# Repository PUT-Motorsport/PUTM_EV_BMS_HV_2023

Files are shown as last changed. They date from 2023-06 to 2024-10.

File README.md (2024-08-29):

# PUTM_EV_BMS_HV_MASTER_2023
Accumulator Managment System (High Voltage Battery Managment System)

## Overview
The AMS system consists of two main parts, the master and multiple slaves.
<p align="center">
  
</p>
The apparatus is responsible for the managment of the battery as a whole, determining it's states like: state of charge or unsafe state plausibility. It also supervises the turning on and off of the hv bus.

## Master
The AMS Master is the center of the whole system it's responsible for most of the tasks: current measurement, high voltage relay control, slave control, high voltage measurement and communication with the car. 
<p align="center"> 
  
</p>

### Software
The AMS system havely relies on RTOS (Real Time Operating System) for seperating and managing different tasks. The system is divided mainly into three parts:
- main task - responsible for control over the whole system,
- subsidiary tasks - for off handling time consuming calculations or interfacing,
- communication tasks - for handling communication with external systems like CAN communication with the car or isoSPI for communication with the slaves.

### Hardware 
The AMS is powered by STM32G484xx, a powerful, new gen MCU capable of handling varius communication interfaces and tasks. On board there are also three 24bit ADC ICs responsible for taking precise measurments of flowing current and voltage present on HV bus. For interfacing with other components the AMS uses M80 and M300 series Harwin connectors which offer high reliability. The board also features other logic components all on a custom 4 layer board.

<p align="center"> 
  
</p>

### The research and development work was carried out was a part of the Student Scientific Clubs Create Innovations (SKNTI) program. [Ministry of Science and Higher Education](https://www.gov.pl/web/nauka)
baner-sknti

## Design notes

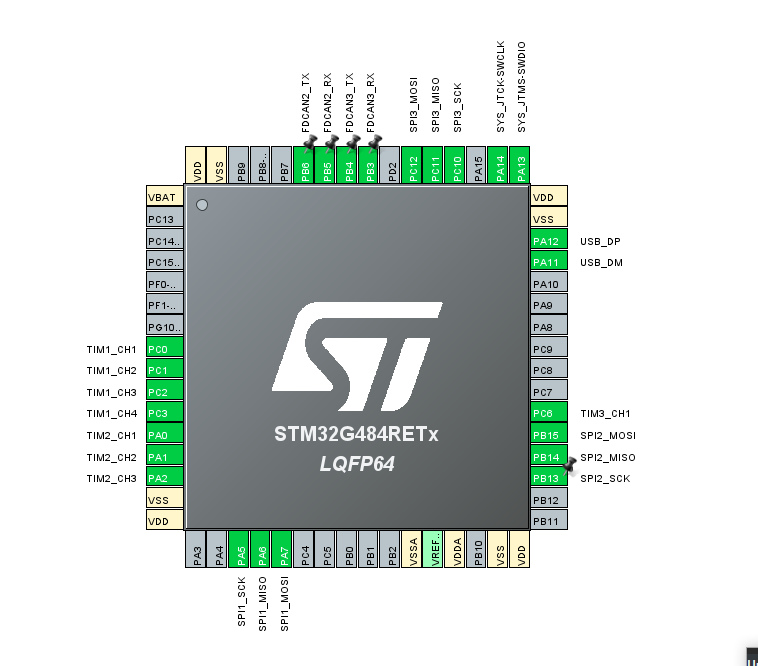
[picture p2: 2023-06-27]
hardware/images/Zrzut ekranu 2023-05-05 002628.png

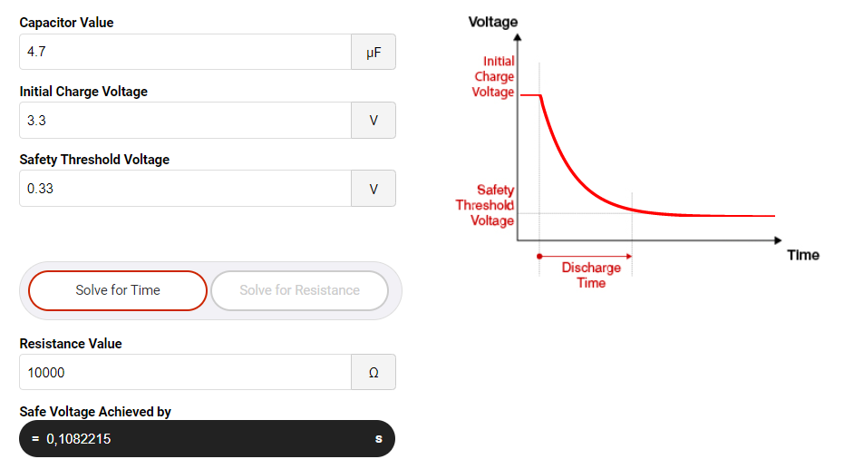
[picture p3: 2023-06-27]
hardware/images/peak_generator_graph.png

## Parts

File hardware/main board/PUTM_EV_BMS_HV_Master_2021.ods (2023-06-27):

Source: | C:\Users\Tomek\Desktop\PUTM\2021\BMS master\PUTM_EV_BMS_HV_Master_2021\PUTM_EV_BMS_HV_Master_2021.sch
Date: | 21.05.2021 00:54:58
Tool: | Eeschema (5.1.5)-3
Generator: | C:\Program Files\KiCad\bin\scripting\plugins/bom_csv_grouped_by_value.py
Component Count: | 206
Individual Components:
Item | Qty | Reference(s) | Value | LibPart | Footprint | Datasheet | MF | PARTREV | STANDART
 |  | BT1 | KEYSTONE 103 | Device:Battery_Cell | Battery:BatteryHolder_Keystone_103_1x20mm | ~
 |  | C1 | 100nF | Device:C | Capacitor_SMD:C_0603_1608Metric | ~
 |  | C2 | 680uF/35V | Device:CP_Small | Capacitor_SMD:CP_Elec_8x10 | ~
 |  | C3 | 4.7uF | Device:C_Small | Capacitor_SMD:C_0603_1608Metric | ~
 |  | C4 | 100nF | Device:C | Capacitor_SMD:C_0603_1608Metric | ~
 |  | C5 | 4.7uF | Device:C_Small | Capacitor_SMD:C_0603_1608Metric | ~
 |  | C6 | 1nF/1kV | Device:C | Capacitor_SMD:C_1206_3216Metric | ~
 |  | C7 | 1nF/1kV | Device:C | Capacitor_SMD:C_1206_3216Metric | ~
 |  | C8 | 220uF/35V | Device:CP_Small | Capacitor_SMD:CP_Elec_8x10 | ~
 |  | C9 | 10uF | Device:C_Small | Capacitor_SMD:C_0603_1608Metric | ~
 |  | C10 | 10uF | Device:C_Small | Capacitor_SMD:C_0603_1608Metric | ~
 |  | C11 | 100nF | Device:C | Capacitor_SMD:C_0603_1608Metric | ~
 |  | C12 | 100nF | Device:C | Capacitor_SMD:C_0603_1608Metric | ~
 |  | C13 | 1uF | Device:C_Small | Capacitor_SMD:C_0603_1608Metric | ~
 |  | C14 | 1uF | Device:C_Small | Capacitor_SMD:C_0603_1608Metric | ~
 |  | C15 | 100nF | Device:C_Small | Capacitor_SMD:C_0603_1608Metric | ~
 |  | C16 | 1uF | Device:C_Small | Capacitor_SMD:C_0603_1608Metric | ~
 |  | C17 | 1uF | Device:C_Small | Capacitor_SMD:C_0603_1608Metric | ~
 |  | C18 | 100nF | Device:C | Capacitor_SMD:C_0603_1608Metric | ~
 |  | C19 | 100nF | Device:C_Small | Capacitor_SMD:C_0603_1608Metric | ~
 |  | C20 | 100nF | Device:C_Small | Capacitor_SMD:C_0603_1608Metric | ~
 |  | C21 | 22pF | Device:C_Small | Capacitor_SMD:C_0805_2012Metric | ~
 |  | C22 | 22pF | Device:C_Small | Capacitor_SMD:C_0805_2012Metric | ~
 |  | C23 | 10uF | Device:C_Small | Capacitor_SMD:C_0603_1608Metric | ~
 |  | C24 | 4.7uF | Device:C_Small | Capacitor_SMD:C_0603_1608Metric | ~
 |  | C25 | 1uF | Device:C_Small | Capacitor_SMD:C_0603_1608Metric | ~
 |  | C26 | 100nF | Device:C_Small | Capacitor_SMD:C_0603_1608Metric | ~
 |  | C27 | 100nF | Device:C_Small | Capacitor_SMD:C_0603_1608Metric | ~
 |  | C28 | 100nF | Device:C_Small | Capacitor_SMD:C_0603_1608Metric | ~
 |  | C29 | 10uF | Device:C_Small | Capacitor_SMD:C_0603_1608Metric | ~
 |  | C30 | 10uF | Device:C_Small | Capacitor_SMD:C_0603_1608Metric | ~
 |  | C31 | 100nF | Device:C_Small | Capacitor_SMD:C_0603_1608Metric | ~
 |  | C32 | 10uF | Device:C_Small | Capacitor_SMD:C_0603_1608Metric | ~
 |  | C33 | 1uF | Device:C_Small | Capacitor_SMD:C_0603_1608Metric | ~
 |  | C34 | 4.7uF | Device:C_Small | Capacitor_SMD:C_0603_1608Metric | ~
 |  | C35 | 100nF | Device:C_Small | Capacitor_SMD:C_0603_1608Metric | ~
 |  | C36 | 100nF | Device:C_Small | Capacitor_SMD:C_0603_1608Metric | ~
 |  | C37 | 100nF | Device:C_Small | Capacitor_SMD:C_0603_1608Metric | ~
 |  | C38 | 1uF | Device:C_Small | Capacitor_SMD:C_0603_1608Metric | ~
 |  | C39 | 100uF/35V | Device:CP_Small | Capacitor_Tantalum_SMD:CP_EIA-3216-18_Kemet-A | ~
 |  | C40 | 100nF | Device:C_Small | Capacitor_SMD:C_0603_1608Metric | ~
 |  | C41 | 10nF | Device:C_Small | Capacitor_SMD:C_0603_1608Metric | ~
 |  | C42 | 4.7uF | Device:C_Small | Capacitor_SMD:C_0603_1608Metric | ~
 |  | C43 | 27pF | Device:C_Small | Capacitor_SMD:C_0603_1608Metric | ~
 |  | C44 | 10nF | Device:C_Small | Capacitor_SMD:C_0603_1608Metric | ~
 |  | C45 | 27pF | Device:C_Small | Capacitor_SMD:C_0603_1608Metric | ~
 |  | C46 | 10nF | Device:C_Small | Capacitor_SMD:C_0603_1608Metric | ~
 |  | C47 | 100nF | Device:C_Small | Capacitor_SMD:C_0603_1608Metric | ~
 |  | C48 | 10nF | Device:C_Small | Capacitor_SMD:C_0603_1608Metric | ~
 |  | C49 | 10nF | Device:C_Small | Capacitor_SMD:C_0603_1608Metric | ~
 |  | C50 | 100nF | Device:C_Small | Capacitor_SMD:C_0603_1608Metric | ~
 |  | C51 | 100nF | Device:C_Small | Capacitor_SMD:C_0603_1608Metric | ~
 |  | C52 | 22pF | Device:C_Small | Capacitor_SMD:C_0805_2012Metric | ~
 |  | C53 | 22pF | Device:C_Small | Capacitor_SMD:C_0805_2012Metric | ~
 |  | C54 | 100nF | Device:C_Small | Capacitor_SMD:C_0603_1608Metric | ~
 |  | D1 | 3A | Device:D_Schottky_Small_ALT | Diode_SMD:D_SMA | ~
 |  | D2 | BAT54C | Diode:BAT54C | Package_TO_SOT_SMD:SOT-23 | http://www.diodes.com/_files/datasheets/ds11005.pdf
 |  | D3 | BAT54C | Diode:BAT54C | Package_TO_SOT_SMD:SOT-23 | http://www.diodes.com/_files/datasheets/ds11005.pdf
 |  | D4 | D_TVS 30V | Device:D_TVS | Diode_SMD:D_SMA | ~
 |  | D5 | D_TVS 5V | Device:D_TVS | Diode_SMD:D_SMA | ~
 |  | D6 | D_TVS 5V | Device:D_TVS | Diode_SMD:D_SMA | ~
 |  | D7 | LED_Small_ALT | Device:LED_Small_ALT | LED_SMD:LED_0603_1608Metric | ~
 |  | D8 | LED_Small_ALT | Device:LED_Small_ALT | LED_SMD:LED_0603_1608Metric | ~
 |  | D9 | LED_Small_ALT | Device:LED_Small_ALT | LED_SMD:LED_0603_1608Metric | ~
 |  | D10 | PESD2CAN.215 | Device:D_TVS_x2_AAC | Package_TO_SOT_SMD:SOT-23 | ~
 |  | F1 | 0.5A | Device:Fuse_Small | Fuse:Fuse_1206_3216Metric | ~
 |  | F2 | 1A | Device:Fuse_Small | Fuse:Fuse_1206_3216Metric | ~
 |  | FB1 | ferrite_baud | Device:Ferrite_Bead_Small | Inductor_SMD:L_0603_1608Metric | ~
 |  | J1 | Conn_01x04 | Connector_Generic:Conn_01x04 | TerminalBlock_TE-Connectivity:TerminalBlock_TE_282834-4_1x04_P2.54mm_Horizontal | ~
 |  | J2 | Conn_01x02 | Connector_Generic:Conn_01x02 | TerminalBlock_TE-Connectivity:TerminalBlock_TE_282834-2_1x02_P2.54mm_Horizontal | ~
 |  | J3 | Conn_01x02 | Connector_Generic:Conn_01x02 | TerminalBlock_TE-Connectivity:TerminalBlock_TE_282834-2_1x02_P2.54mm_Horizontal | ~
 |  | J4 | Conn_01x02 | Connector_Generic:Conn_01x02 | TerminalBlock_TE-Connectivity:TerminalBlock_TE_282834-2_1x02_P2.54mm_Horizontal | ~
 |  | J5 | Conn_01x04 | Connector_Generic:Conn_01x04 | TerminalBlock_TE-Connectivity:TerminalBlock_TE_282834-4_1x04_P2.54mm_Horizontal | ~
 |  | J6 | PWR | Connector_Generic:Conn_01x02 | TerminalBlock_TE-Connectivity:TerminalBlock_TE_282834-2_1x02_P2.54mm_Horizontal | ~
 |  | J7 | Conn_01x02 | Connector_Generic:Conn_01x02 | TerminalBlock_TE-Connectivity:TerminalBlock_TE_282834-2_1x02_P2.54mm_Horizontal | ~
 |  | J8 | Conn_01x02 | Connector_Generic:Conn_01x02 | TerminalBlock_TE-Connectivity:TerminalBlock_TE_282834-2_1x02_P2.54mm_Horizontal | ~
 |  | J9 | Conn_01x02 | Connector_Generic:Conn_01x02 | TerminalBlock_TE-Connectivity:TerminalBlock_TE_282834-2_1x02_P2.54mm_Horizontal | ~
 |  | J10 | Micro_SD_Card_Det_Hirose_DM3AT | Connector:Micro_SD_Card_Det_Hirose_DM3AT | Connector_Card:microSD_HC_Hirose_DM3AT-SF-PEJM5 | https://www.hirose.com/product/en/download_file/key_name/DM3/category/Catalog/doc_file_id/49662/?item_id=195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
 |  | J11 | Conn_01x04 | Connector_Generic:Conn_01x04 | TerminalBlock_TE-Connectivity:TerminalBlock_TE_282834-4_1x04_P2.54mm_Horizontal | ~
 |  | J12 | USB_B_Mini | Connector:USB_B_Mini | Connector_USB:USB_Mini-B_Lumberg_2486_01_Horizontal | ~
 |  | J13 | Conn_01x03 | Connector_Generic:Conn_01x03 | Connector_Molex:Molex_Micro-Fit_3.0_43650-0315_1x03_P3.00mm_Vertical | ~
 |  | J14 | Conn_01x03 | Connector_Generic:Conn_01x03 | Connector_Molex:Molex_Micro-Fit_3.0_43650-0315_1x03_P3.00mm_Vertical | ~
 |  | J15 | Conn_01x05 | Connector_Generic:Conn_01x05 | Connector_PinHeader_2.54mm:PinHeader_1x05_P2.54mm_Vertical | ~
 |  | J16 | CAN | Connector_Generic:Conn_01x02 | TerminalBlock_TE-Connectivity:TerminalBlock_TE_282834-2_1x02_P2.54mm_Horizontal | ~
 |  | K1 | FINDER-30.22 | Relay:FINDER-30.22 | Relay_THT:Relay_DPDT_Finder_30.22 | http://gfinder.findernet.com/assets/Series/354/S30EN.pdf
 |  | K2 | ALDP105W | PUTM_EV_BMS_library:ALDP105W | RELAY_ALDP105W |  | Panasonic | N/A | Manufacturer Recommendations
 |  | K3 | ALDP105W | PUTM_EV_BMS_library:ALDP105W | RELAY_ALDP105W |  | Panasonic | N/A | Manufacturer Recommendations
 |  | K4 | ALDP105W | PUTM_EV_BMS_library:ALDP105W | RELAY_ALDP105W |  | Panasonic | N/A | Manufacturer Recommendations
 |  | L1 | 6.8uH | Device:L | Inductor_SMD:L_1206_3216Metric | ~
 |  | L2 | 6.8uH | Device:L | Inductor_SMD:L_1206_3216Metric | ~
 |  | L3 | 110uH | Device:L_Small | Inductor_SMD:L_1206_3216Metric | ~
 |  | L4 | NLV32T-220J-PF | Device:L_Small | Inductor_SMD:L_1210_3225Metric | ~
 |  | P1 | AM1LS-0505S-NZ | PUTM_EV_BMS_library:AM1LS-0505S-NZ | Converter_DCDC:Converter_DCDC_TRACO_TMR-1SM_SMD | https://www.tme.eu/Document/eb524b8882472c891796e11a1a1007e6/am1ls-%28j%29nz.pdf
 |  | P2 | AM1LS-0505S-NZ | PUTM_EV_BMS_library:AM1LS-0505S-NZ | Converter_DCDC:Converter_DCDC_TRACO_TMR-1SM_SMD | https://www.tme.eu/Document/eb524b8882472c891796e11a1a1007e6/am1ls-%28j%29nz.pdf
 |  | Q1 | 2N7002 | Transistor_FET:2N7002 | Package_TO_SOT_SMD:SOT-23 | https://www.fairchildsemi.com/datasheets/2N/2N7002.pdf
 |  | Q2 | 2N7002 | Transistor_FET:2N7002 | Package_TO_SOT_SMD:SOT-23 | https://www.fairchildsemi.com/datasheets/2N/2N7002.pdf
 |  | Q3 | 2N7002 | Transistor_FET:2N7002 | Package_TO_SOT_SMD:SOT-23 | https://www.fairchildsemi.com/datasheets/2N/2N7002.pdf
 |  | Q4 | 2N7002 | Transistor_FET:2N7002 | Package_TO_SOT_SMD:SOT-23 | https://www.fairchildsemi.com/datasheets/2N/2N7002.pdf
 |  | R1 | 220k | Device:R | Resistor_SMD:R_0603_1608Metric | ~
 |  | R2 | 220k | Device:R | Resistor_SMD:R_0603_1608Metric | ~
 |  | R3 | 220k | Device:R | Resistor_SMD:R_0603_1608Metric | ~
 |  | R4 | 220k | Device:R | Resistor_SMD:R_0603_1608Metric | ~
 |  | R5 | 220k | Device:R | Resistor_SMD:R_0603_1608Metric | ~
 |  | R6 | 220k | Device:R | Resistor_SMD:R_0603_1608Metric | ~
 |  | R7 | 220k | Device:R | Resistor_SMD:R_0603_1608Metric | ~
 |  | R8 | 220k | Device:R | Resistor_SMD:R_0603_1608Metric | ~
 |  | R9 | 2,2k | Device:R | Resistor_SMD:R_0603_1608Metric | ~
 |  | R10 | 2,2k | Device:R | Resistor_SMD:R_0603_1608Metric | ~
 |  | R11 | 0 | Device:R | Resistor_SMD:R_0603_1608Metric | ~
 |  | R12 | 0 | Device:R | Resistor_SMD:R_0603_1608Metric | ~
 |  | R13 | 220 | Device:R | Resistor_SMD:R_0603_1608Metric | ~
 |  | R14 | 220 | Device:R | Resistor_SMD:R_0603_1608Metric | ~
 |  | R15 | 10k | Device:R_Small | Resistor_SMD:R_0603_1608Metric | ~
 |  | R16 | 10k | Device:R_Small | Resistor_SMD:R_0603_1608Metric | ~
 |  | R17 | 10k | Device:R_Small | Resistor_SMD:R_0603_1608Metric | ~
 |  | R18 | 10k | Device:R_Small | Resistor_SMD:R_0603_1608Metric | ~
 |  | R19 | 22k | Device:R_Small | Resistor_SMD:R_0603_1608Metric | ~
 |  | R20 | 22k | Device:R_Small | Resistor_SMD:R_0603_1608Metric | ~
 |  | R21 | 22k | Device:R_Small | Resistor_SMD:R_0603_1608Metric | ~
 |  | R22 | 22k | Device:R_Small | Resistor_SMD:R_0603_1608Metric | ~
 |  | R23 | 160 | Device:R_Small | Resistor_SMD:R_0603_1608Metric | ~
 |  | R24 | 160 | Device:R_Small | Resistor_SMD:R_0603_1608Metric | ~
 |  | R25 | 10K | Device:R_Small | Resistor_SMD:R_0603_1608Metric | ~
 |  | R26 | 10K | Device:R_Small | Resistor_SMD:R_0603_1608Metric | ~
 |  | R27 | 10K | Device:R_Small | Resistor_SMD:R_0603_1608Metric | ~
 |  | R28 | 10K | Device:R_Small | Resistor_SMD:R_0603_1608Metric | ~
 |  | R29 | 160 | Device:R_Small | Resistor_SMD:R_0603_1608Metric | ~
 |  | R30 | 10K | Device:R_Small | Resistor_SMD:R_0603_1608Metric | ~
 |  | R31 | 10K | Device:R_Small | Resistor_SMD:R_0603_1608Metric | ~
 |  | R32 | 10K | Device:R_Small | Resistor_SMD:R_0603_1608Metric | ~
 |  | R33 | 10K | Device:R_Small | Resistor_SMD:R_0603_1608Metric | ~
 |  | R34 | 10K | Device:R_Small | Resistor_SMD:R_0603_1608Metric | ~
 |  | R35 | 1K | Device:R_Small | Resistor_SMD:R_0603_1608Metric | ~
 |  | R36 | 1K | Device:R_Small | Resistor_SMD:R_0603_1608Metric | ~
 |  | R37 | 1K | Device:R_Small | Resistor_SMD:R_0603_1608Metric | ~
 |  | R38 | 1K | Device:R_Small | Resistor_SMD:R_0603_1608Metric | ~
 |  | R39 | 10k | Device:R_Small | Resistor_SMD:R_0603_1608Metric | ~
 |  | R40 | 100 | Device:R_Small | Resistor_SMD:R_0603_1608Metric | ~
 |  | R41 | 100k | Device:R_Small | Resistor_SMD:R_0603_1608Metric | ~
 |  | R42 | 22k | Device:R_Small | Resistor_SMD:R_0603_1608Metric | ~
 |  | R43 | 10k | Device:R_Small | Resistor_SMD:R_0603_1608Metric | ~
 |  | R44 | 0 | Device:R_Small | Resistor_SMD:R_0603_1608Metric | ~
 |  | R45 | 10k | Device:R_Small | Resistor_SMD:R_0603_1608Metric | ~
 |  | R46 | 10k | Device:R_Small | Resistor_SMD:R_0603_1608Metric | ~
 |  | R47 | 100 | Device:R_Small | Resistor_SMD:R_0603_1608Metric | ~
 |  | R48 | 100 | Device:R_Small | Resistor_SMD:R_0603_1608Metric | ~
 |  | R49 | 10k | Device:R_Small | Resistor_SMD:R_0603_1608Metric | ~
 |  | R50 | 10k | Device:R_Small | Resistor_SMD:R_0603_1608Metric | ~
 |  | R51 | 0 | Device:R_Small | Resistor_SMD:R_0603_1608Metric | ~
 |  | R52 | 100k | Device:R_Small | Resistor_SMD:R_0603_1608Metric | ~
 |  | R53 | 10k | Device:R_Small | Resistor_SMD:R_0603_1608Metric | ~
 |  | R54 | 1k | Device:R_Small | Resistor_SMD:R_0603_1608Metric | ~
 |  | R55 | 10k | Device:R_Small | Resistor_SMD:R_0603_1608Metric | ~
 |  | R56 | 10k | Device:R_Small | Resistor_SMD:R_0603_1608Metric | ~
 |  | R57 | 10k | Device:R_Small | Resistor_SMD:R_0603_1608Metric | ~
 |  | R58 | 10k | Device:R_Small | Resistor_SMD:R_0603_1608Metric | ~
 |  | R59 | 10k | Device:R_Small | Resistor_SMD:R_0603_1608Metric | ~
 |  | R60 | 10k | Device:R_Small | Resistor_SMD:R_0603_1608Metric | ~
 |  | R61 | 10k | Device:R_Small | Resistor_SMD:R_0603_1608Metric | ~
 |  | R62 | 10K | Device:R_Small | Resistor_SMD:R_0603_1608Metric | ~
 |  | R63 | 10K | Device:R_Small | Resistor_SMD:R_0603_1608Metric | ~
 |  | R64 | 10K | Device:R_Small | Resistor_SMD:R_0603_1608Metric | ~
 |  | R65 | 10K | Device:R_Small | Resistor_SMD:R_0603_1608Metric | ~
 |  | R66 | 3.3k | Device:R | Resistor_SMD:R_0603_1608Metric | ~
 |  | R67 | 3.3k | Device:R | Resistor_SMD:R_0603_1608Metric | ~
 |  | R68 | 3.3k | Device:R | Resistor_SMD:R_0603_1608Metric | ~
 |  | R69 | 10K | Device:R_Small | Resistor_SMD:R_0603_1608Metric | ~
 |  | R70 | 10k | Device:R | Resistor_SMD:R_0603_1608Metric | ~
 |  | R71 | 10K | Device:R_Small | Resistor_SMD:R_0603_1608Metric | ~
 |  | R72 | 10k | Device:R | Resistor_SMD:R_0603_1608Metric | ~
 |  | R73 | 100k | Device:R_Small | Resistor_SMD:R_0603_1608Metric | ~
 |  | R74 | 27R | Device:R_Small | Resistor_SMD:R_0603_1608Metric | ~
 |  | R75 | 27R | Device:R_Small | Resistor_SMD:R_0603_1608Metric | ~
 |  | R76 | 49.9R | Device:R_Small | Resistor_SMD:R_0603_1608Metric | ~
 |  | R77 | 49.9R | Device:R_Small | Resistor_SMD:R_0603_1608Metric | ~
 |  | R78 | 49.9R | Device:R_Small | Resistor_SMD:R_0603_1608Metric | ~
 |  | R79 | 49.9R | Device:R_Small | Resistor_SMD:R_0603_1608Metric | ~
 |  | R80 | 10M | Device:R_Small | Resistor_SMD:R_0603_1608Metric | ~
 |  | R81 | 10k | Device:R_Small | Resistor_SMD:R_0603_1608Metric | ~
 |  | R82 | 10k | Device:R_Small | Resistor_SMD:R_0603_1608Metric | ~
 |  | R83 | 10M | Device:R_Small | Resistor_SMD:R_0603_1608Metric | ~
 |  | R84 | 1k | Device:R_Small | Resistor_SMD:R_0603_1608Metric | ~
 |  | R85 | 1k | Device:R_Small | Resistor_SMD:R_0603_1608Metric | ~
 |  | R86 | 1k | Device:R_Small | Resistor_SMD:R_0603_1608Metric | ~
 |  | R87 | 120 | Device:R_Small | Resistor_SMD:R_0603_1608Metric | ~
 |  | SW1 | RESET | Switch:SW_Push | Button_Switch_THT:SW_PUSH_6mm_H5mm | ~
 |  | T1 | HX1188NL | PUTM_EV_BMS_library:HX1188NL | Transformer_SMD:Transformer_Pulse_H1100NL
 |  | U1 | LM2596S-5 | Regulator_Switching:LM2596S-5 | Package_TO_SOT_SMD:TO-263-5_TabPin3 | http://www.ti.com/lit/ds/symlink/lm2596.pdf
 |  | U2 | AMC1311DWV | PUTM_EV_BMS_library:AMC1311DWV | Package_SO:SOIC-8_7.5x5.85mm_P1.27mm | https://www.ti.com/lit/ds/symlink/amc1311.pdf?ts=1610792186113
 |  | U3 | AMC1311DWV | PUTM_EV_BMS_library:AMC1311DWV | Package_SO:SOIC-8_7.5x5.85mm_P1.27mm | https://www.ti.com/lit/ds/symlink/amc1311.pdf?ts=1610792186113
 |  | U4 | MCP6002-I/MS | Amplifier_Operational:MCP6002-xMS | Package_SO:SO-8_3.9x4.9mm_P1.27mm | http://ww1.microchip.com/downloads/en/DeviceDoc/21733j.pdf
 |  | U5 | LM1117-3.3 | Regulator_Linear:LM1117-3.3 | Package_TO_SOT_SMD:SOT-223-3_TabPin2 | http://www.ti.com/lit/ds/symlink/lm1117.pdf
 |  | U6 | LTC6820IMS | PUTM_EV_BMS_library:LTC6820IMS | Package_SO:MSOP-16_3x4.039mm_P0.5mm
 |  | U7 | LTC6820IMS | PUTM_EV_BMS_library:LTC6820IMS | Package_SO:MSOP-16_3x4.039mm_P0.5mm
 |  | U8 | MCP6002-I/MS | Amplifier_Operational:MCP6002-xSN | Package_SO:SO-8_3.9x4.9mm_P1.27mm | http://ww1.microchip.com/downloads/en/DeviceDoc/21733j.pdf
 |  | U9 | STM32F446RETx | MCU_ST_STM32F4:STM32F446RETx | Package_QFP:LQFP-64_10x10mm_P0.5mm | http://www.st.com/st-web-ui/static/active/en/resource/technical/document/datasheet/DM00141306.pdf
 |  | U10 | AT45DB641E-SHN-T | PUTM_EV_BMS_library:AT45DB641E-SHN-T | Package_SO:SOIC-8_5.23x5.23mm_P1.27mm | https://www.tme.eu/Document/f45b2c566e3fa2479856fbfc9ee4fea2/AT45DB641E-DTE.pdf
 |  | U11 | 74LVC1G79GV.125 | 74xGxx:74LVC1G79 | Package_TO_SOT_SMD:SOT-23-5 | http://www.ti.com/lit/sg/scyt129e/scyt129e.pdf
 |  | U12 | PC817 | Isolator:PC817 | Package_DIP:DIP-4_W7.62mm | http://www.soselectronic.cz/a_info/resource/d/pc817.pdf
 |  | U13 | PC817 | Isolator:PC817 | Package_DIP:DIP-4_W7.62mm | http://www.soselectronic.cz/a_info/resource/d/pc817.pdf
 |  | U14 | PC817 | Isolator:PC817 | Package_DIP:DIP-4_W7.62mm | http://www.soselectronic.cz/a_info/resource/d/pc817.pdf
 |  | U15 | FT230XS | Interface_USB:FT230XS | Package_SO:SSOP-16_3.9x4.9mm_P0.635mm | https://www.ftdichip.com/Support/Documents/DataSheets/ICs/DS_FT230X.pdf
 |  | U16 | ADuM1281CRZ | Isolator:ADuM1201CR | Package_SO:SOIC-8_3.9x4.9mm_P1.27mm | https://www.analog.com/static/imported-files/data_sheets/ADuM1200_1201.pdf
 |  | U17 | MCP2562-E-SN | Interface_CAN_LIN:MCP2562-E-SN | Package_SO:SOIC-8_3.9x4.9mm_P1.27mm | http://ww1.microchip.com/downloads/en/DeviceDoc/25167A.pdf
 |  | Y1 | 8MHz | Device:Crystal_Small | Crystal:Crystal_HC49-4H_Vertical | ~
 |  | Y2 | 32.768kHz | Device:Crystal_Small | Crystal:Crystal_HC49-4H_Vertical | ~
Collated Components:
Item | Qty | Reference(s) | Value | LibPart | Footprint | Datasheet | MF | PARTREV | STANDART
1 | 1 | BT1 | KEYSTONE 103 | Device:Battery_Cell | Battery:BatteryHolder_Keystone_103_1x20mm | ~
2 | 5 | C1, C4, C11, C12, C18 | 100nF | Device:C | Capacitor_SMD:C_0603_1608Metric | ~
3 | 1 | C2 | 680uF/35V | Device:CP_Small |  | ~
4 | 5 | C3, C5, C24, C34, C42 | 4.7uF | Device:C_Small | Capacitor_SMD:C_0603_1608Metric | ~
5 | 2 | C6, C7 | 1nF/1kV | Device:C | Capacitor_SMD:C_1206_3216Metric | ~
6 | 1 | C8 | 220uF/35V | Device:CP_Small |  | ~
7 | 6 | C9, C10, C23, C29, C30, C32 | 10uF | Device:C_Small | Capacitor_SMD:C_0603_1608Metric | ~
8 | 7 | C13, C14, C16, C17, C25, C33, C38 | 1uF | Device:C_Small | Capacitor_SMD:C_0603_1608Metric | ~
9 | 15 | C15, C19, C20, C26, C27, C28, C31, C35, C36, C37, C40, C47, C50, C51, C54 | 100nF | Device:C_Small | Capacitor_SMD:C_0603_1608Metric | ~
10 | 4 | C21, C22, C52, C53 | 22pF | Device:C_Small | Capacitor_SMD:C_0603_1608Metric | ~
11 | 1 | C39 | 100uF/35V | Device:CP_Small |  | ~
12 | 5 | C41, C44, C46, C48, C49 | 10nF | Device:C_Small | Capacitor_SMD:C_0603_1608Metric | ~
13 | 2 | C43, C45 | 27pF | Device:C_Small | Capacitor_SMD:C_0603_1608Metric | ~
14 | 1 | D1 | 3A | Device:D_Schottky_Small_ALT | Diode_SMD:D_SMA | ~
15 | 2 | D2, D3 | BAT54C | Diode:BAT54C | Package_TO_SOT_SMD:SOT-23 | http://www.diodes.com/_files/datasheets/ds11005.pdf
16 | 1 | D4 | D_TVS 30V | Device:D_TVS | Diode_SMD:D_SMA | ~
17 | 2 | D5, D6 | D_TVS 5V | Device:D_TVS | Diode_SMD:D_SMA | ~
18 | 3 | D7, D8, D9 | LED_Small_ALT | Device:LED_Small_ALT | LED_SMD:LED_0603_1608Metric | ~
19 | 1 | D10 | PESD2CAN.215 | Device:D_TVS_x2_AAC | Package_TO_SOT_SMD:SOT-23 | ~
20 | 1 | F1 | 0.5A | Device:Fuse_Small | Fuse:Fuse_1206_3216Metric | ~
21 | 1 | F2 | 1A | Device:Fuse_Small | Fuse:Fuse_1206_3216Metric | ~
22 | 1 | FB1 | ferrite_baud | Device:Ferrite_Bead_Small | Inductor_SMD:L_0603_1608Metric | ~
23 | 3 | J1, J5, J11 | Conn_01x04 | Connector_Generic:Conn_01x04 | TerminalBlock_TE-Connectivity:TerminalBlock_TE_282834-4_1x04_P2.54mm_Horizontal | ~
24 | 6 | J2, J3, J4, J7, J8, J9 | Conn_01x02 | Connector_Generic:Conn_01x02 | TerminalBlock_TE-Connectivity:TerminalBlock_TE_282834-2_1x02_P2.54mm_Horizontal | ~
25 | 1 | J6 | PWR | Connector_Generic:Conn_01x02 | TerminalBlock_TE-Connectivity:TerminalBlock_TE_282834-2_1x02_P2.54mm_Horizontal | ~
26 | 1 | J10 | Micro_SD_Card_Det_Hirose_DM3AT | Connector:Micro_SD_Card_Det_Hirose_DM3AT | Connector_Card:microSD_HC_Hirose_DM3AT-SF-PEJM5 | https://www.hirose.com/product/en/download_file/key_name/DM3/category/Catalog/doc_file_id/49662/?item_id=195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
27 | 1 | J12 | USB_B_Mini | Connector:USB_B_Mini | Connector_USB:USB_Mini-B_Lumberg_2486_01_Horizontal | ~
28 | 2 | J13, J14 | Conn_01x03 | Connector_Generic:Conn_01x03 | Connector_Molex:Molex_Micro-Fit_3.0_43650-0315_1x03_P3.00mm_Vertical | ~
29 | 1 | J15 | Conn_01x05 | Connector_Generic:Conn_01x05 | Connector_PinHeader_2.54mm:PinHeader_1x05_P2.54mm_Vertical | ~
30 | 1 | J16 | CAN | Connector_Generic:Conn_01x02 | TerminalBlock_TE-Connectivity:TerminalBlock_TE_282834-2_1x02_P2.54mm_Horizontal | ~
31 | 1 | K1 | FINDER-30.22 | Relay:FINDER-30.22 | Relay_THT:Relay_DPDT_Finder_30.22 | http://gfinder.findernet.com/assets/Series/354/S30EN.pdf
32 | 3 | K2, K3, K4 | ALDP105W | PUTM_EV_BMS_library:ALDP105W | RELAY_ALDP105W |  | Panasonic | N/A | Manufacturer Recommendations
33 | 2 | L1, L2 | 6.8uH | Device:L | Inductor_SMD:L_1206_3216Metric | ~
34 | 1 | L3 | 110uH | Device:L_Small | Inductor_SMD:L_1206_3216Metric | ~
35 | 1 | L4 | NLV32T-220J-PF | Device:L_Small | Inductor_SMD:L_1210_3225Metric | ~
36 | 2 | P1, P2 | AM1LS-0505S-NZ | PUTM_EV_BMS_library:AM1LS-0505S-NZ | Converter_DCDC:Converter_DCDC_TRACO_TMR-1SM_SMD | https://www.tme.eu/Document/eb524b8882472c891796e11a1a1007e6/am1ls-%28j%29nz.pdf
37 | 4 | Q1, Q2, Q3, Q4 | 2N7002 | Transistor_FET:2N7002 | Package_TO_SOT_SMD:SOT-23 | https://www.fairchildsemi.com/datasheets/2N/2N7002.pdf
38 | 8 | R1, R2, R3, R4, R5, R6, R7, R8 | 200k | Device:R | Resistor_SMD:R_1206 | ~
39 | 2 | R9, R10 | 2,2k | Device:R | Resistor_SMD:R_0603_1608Metric | ~
40 | 2 | R11, R12 | 0 | Device:R | Resistor_SMD:R_0603_1608Metric | ~
41 | 2 | R13, R14 | 200 | Device:R | Resistor_SMD:R_0603_1608Metric | ~
42 | 20 | R15, R16, R17, R18, R39, R43, R45, R46, R49, R50, R53, R55, R56, R57, R58, R59, R60, R61, R81, R82 | 10k | Device:R_Small | Resistor_SMD:R_0603_1608Metric | ~
43 | 5 | R19, R20, R21, R22, R42 | 22k | Device:R_Small | Resistor_SMD:R_0603_1608Metric | ~
44 | 3 | R23, R24, R29 | 100 | Device:R_Small | Resistor_SMD:R_0603_1608Metric | ~
45 | 15 | R25, R26, R27, R28, R30, R31, R32, R33, R34, R62, R63, R64, R65, R69, R71 | 10K | Device:R_Small | Resistor_SMD:R_0603_1608Metric | ~
46 | 4 | R35, R36, R37, R38 | 1K | Device:R_Small | Resistor_SMD:R_0603_1608Metric | ~
47 | 3 | R40, R47, R48 | 100 | Device:R_Small | Resistor_SMD:R_0603_1608Metric | ~
48 | 3 | R41, R52, R73 | 100k | Device:R_Small | Resistor_SMD:R_1206 | ~
49 | 2 | R44, R51 | 0 | Device:R_Small | Resistor_SMD:R_0603_1608Metric | ~
50 | 4 | R54, R84, R85, R86 | 1k | Device:R_Small | Resistor_SMD:R_0603_1608Metric | ~
51 | 3 | R66, R67, R68 | 3.3k | Device:R | Resistor_SMD:R_0603_1608Metric | ~
52 | 2 | R70, R72 | 10k | Device:R | Resistor_SMD:R_0603_1608Metric | ~
53 | 2 | R74, R75 | 27R | Device:R_Small | Resistor_SMD:R_0603_1608Metric | ~
54 | 4 | R76, R77, R78, R79 | 49.9R | Device:R_Small | Resistor_SMD:R_0603_1608Metric | ~
55 | 2 | R80, R83 | 10M | Device:R_Small | Resistor_SMD:R_0603_1608Metric | ~
56 | 1 | R87 | 120 | Device:R_Small | Resistor_SMD:R_0603_1608Metric | ~
57 | 1 | SW1 | RESET | Switch:SW_Push | Button_Switch_THT:SW_PUSH_6mm_H5mm | ~
58 | 1 | T1 | HX1188NL | PUTM_EV_BMS_library:HX1188NL | Transformer_SMD:Transformer_Pulse_H1100NL
59 | 1 | U1 | LM2596S-5 | Regulator_Switching:LM2596S-5 | Package_TO_SOT_SMD:TO-263-5_TabPin3 | http://www.ti.com/lit/ds/symlink/lm2596.pdf
60 | 2 | U2, U3 | AMC1311DWV | PUTM_EV_BMS_library:AMC1311DWV | Package_SO:SOIC-8_7.5x5.85mm_P1.27mm | https://www.ti.com/lit/ds/symlink/amc1311.pdf?ts=1610792186113
61 | 1 | U4 | MCP6002-I/MS | Amplifier_Operational:MCP6002-xMS | Package_SO:SO-8_3.9x4.9mm_P1.27mm | http://ww1.microchip.com/downloads/en/DeviceDoc/21733j.pdf
62 | 1 | U5 | LM1117-3.3 | Regulator_Linear:LM1117-3.3 | Package_TO_SOT_SMD:SOT-223-3_TabPin2 | http://www.ti.com/lit/ds/symlink/lm1117.pdf
63 | 2 | U6, U7 | LTC6820IMS | PUTM_EV_BMS_library:LTC6820IMS | Package_SO:MSOP-16_3x4.039mm_P0.5mm
64 | 1 | U8 | MCP6002-I/MS | Amplifier_Operational:MCP6002-xSN | Package_SO:SO-8_3.9x4.9mm_P1.27mm | http://ww1.microchip.com/downloads/en/DeviceDoc/21733j.pdf
65 | 1 | U9 | STM32F446RETx | MCU_ST_STM32F4:STM32F446RETx | Package_QFP:LQFP-64_10x10mm_P0.5mm | http://www.st.com/st-web-ui/static/active/en/resource/technical/document/datasheet/DM00141306.pdf
66 | 1 | U10 | AT45DB641E-SHN-T | PUTM_EV_BMS_library:AT45DB641E-SHN-T | Package_SO:SOIC-8_5.23x5.23mm_P1.27mm | https://www.tme.eu/Document/f45b2c566e3fa2479856fbfc9ee4fea2/AT45DB641E-DTE.pdf
67 | 1 | U11 | 74LVC1G79GV.125 | 74xGxx:74LVC1G79 | Package_TO_SOT_SMD:SOT-23-5 | http://www.ti.com/lit/sg/scyt129e/scyt129e.pdf
68 | 3 | U12, U13, U14 | PC817 | Isolator:PC817 | Package_DIP:DIP-4_W7.62mm | http://www.soselectronic.cz/a_info/resource/d/pc817.pdf
69 | 1 | U15 | FT230XS | Interface_USB:FT230XS | Package_SO:SSOP-16_3.9x4.9mm_P0.635mm | https://www.ftdichip.com/Support/Documents/DataSheets/ICs/DS_FT230X.pdf
70 | 1 | U16 | ADuM1281CRZ | Isolator:ADuM1201CR | Package_SO:SOIC-8_3.9x4.9mm_P1.27mm | https://www.analog.com/static/imported-files/data_sheets/ADuM1200_1201.pdf
71 | 1 | U17 | MCP2562-E-SN | Interface_CAN_LIN:MCP2562-E-SN | Package_SO:SOIC-8_3.9x4.9mm_P1.27mm | http://ww1.microchip.com/downloads/en/DeviceDoc/25167A.pdf
72 | 1 | Y1 | 8MHz | Device:Crystal_Small | Crystal:Crystal_HC49-4H_Vertical | ~
73 | 1 | Y2 | 32.768kHz | Device:Crystal_Small | Crystal:Crystal_HC49-4H_Vertical | ~

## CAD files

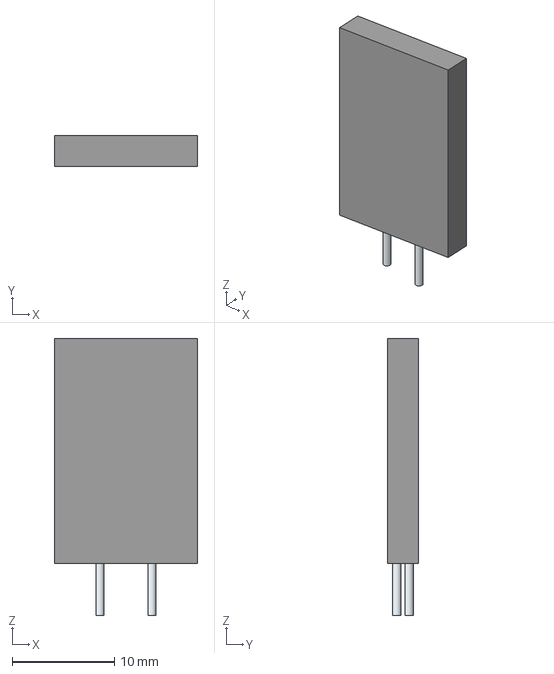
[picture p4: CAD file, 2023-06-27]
hardware/footprint/30R400UMR/30R400UMR.stp
14.0 x 3.00 x 27.1 mm
Leads x 2

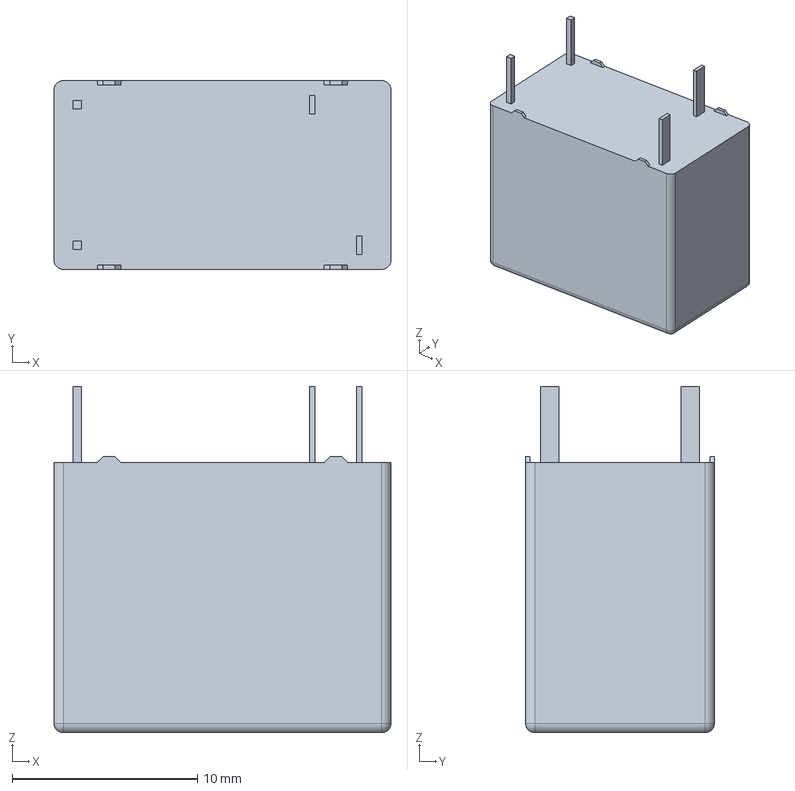
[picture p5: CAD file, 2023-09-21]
hardware/footprint/6-1419128-4/6-1419128-4.stp
18.2 x 10.2 x 18.7 mm

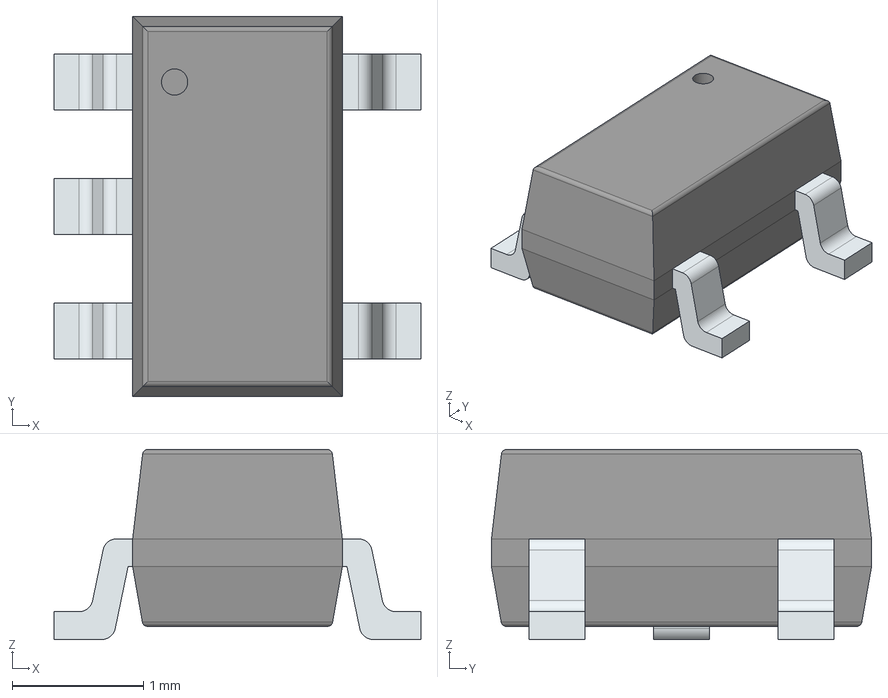
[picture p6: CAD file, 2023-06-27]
hardware/footprint/ADA4505-1ARJZ-R7/ADA4505-1ARJZ-R7.stp
2.80 x 2.90 x 1.45 mm
PinsArrayL
PinsArrayR

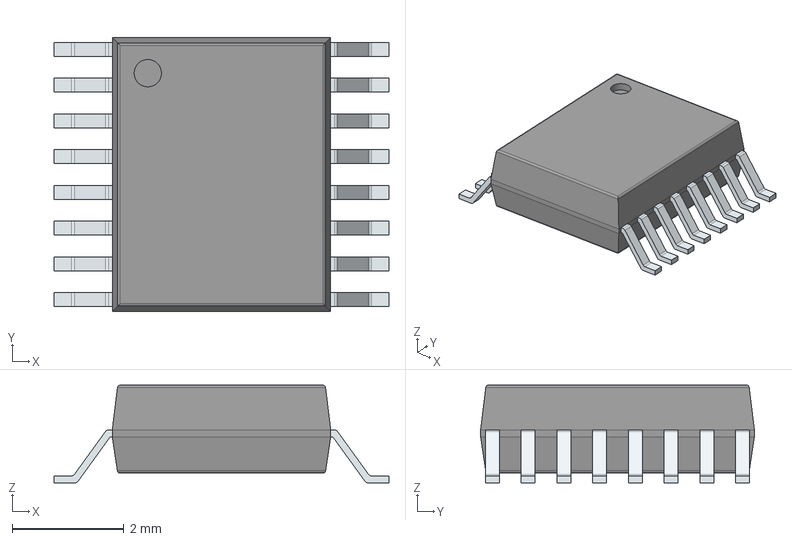
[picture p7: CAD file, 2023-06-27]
hardware/footprint/ADUM7440ARQZ/ADUM7440ARQZ.stp
6.00 x 4.90 x 1.75 mm
PinsArrayLR

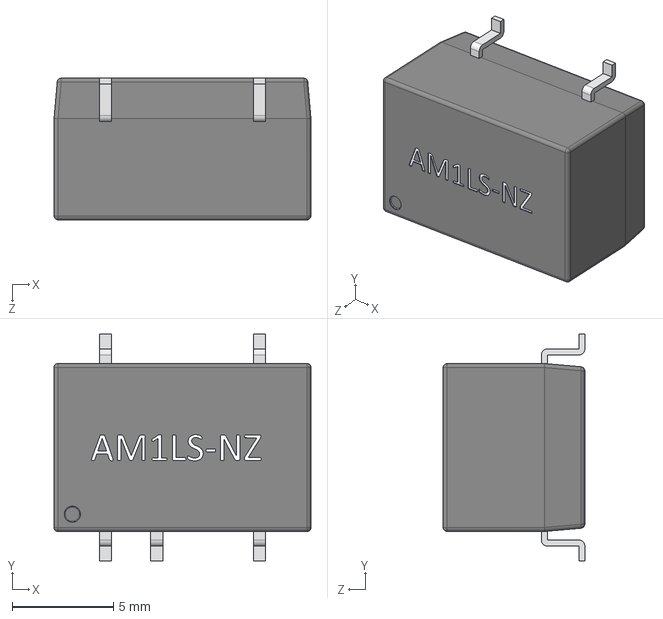
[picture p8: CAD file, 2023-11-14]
hardware/footprint/AM1LS/AM1LS-NZ.step
12.7 x 11.2 x 7.00 mm

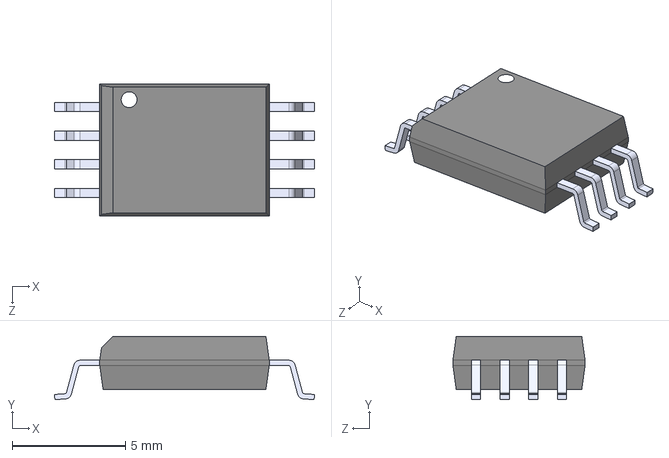
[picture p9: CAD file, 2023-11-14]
hardware/footprint/AMC1331/AMC1311BDWVR.step
11.5 x 2.80 x 5.85 mm

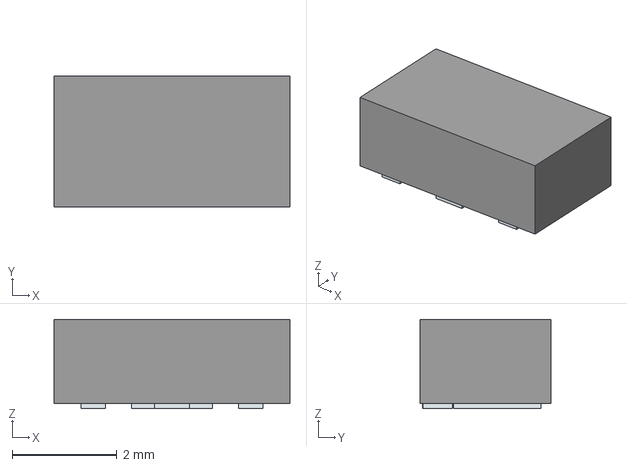
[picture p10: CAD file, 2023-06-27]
hardware/footprint/AP7365-33YRG-13/AP7365-33YRG-13.stp
4.50 x 2.50 x 1.70 mm
Pins

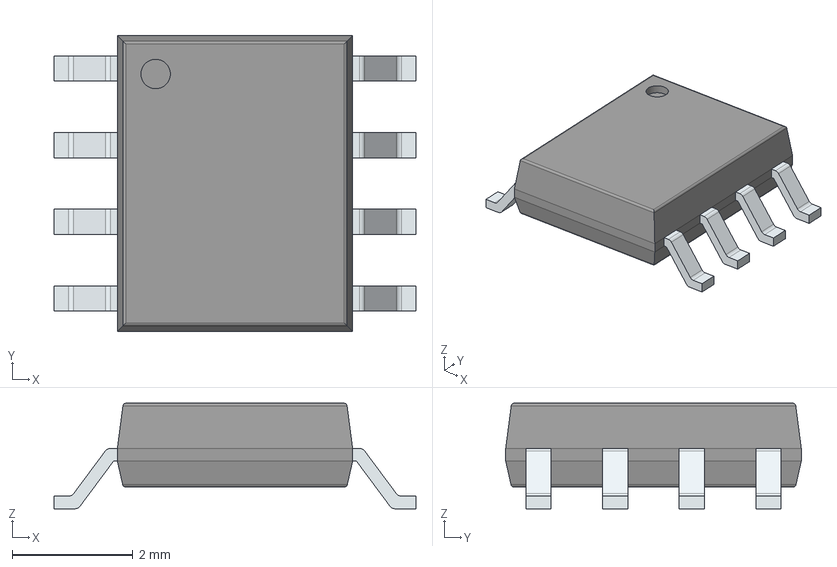
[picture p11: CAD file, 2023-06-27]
hardware/footprint/FOD8802DR2/FOD8802DR2.stp
6.00 x 4.90 x 1.75 mm
PinsArrayLR

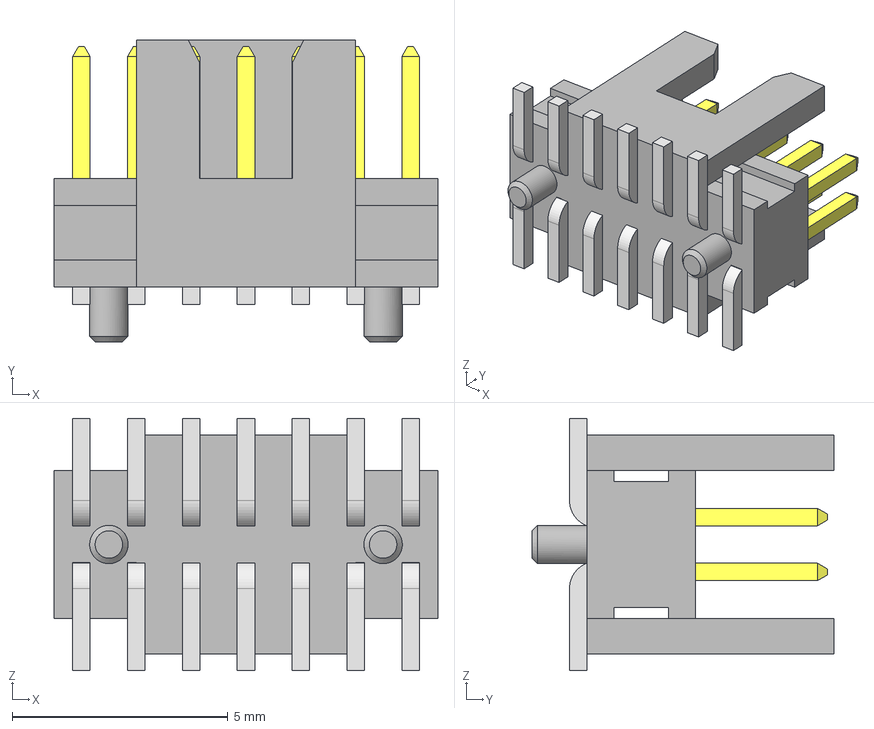
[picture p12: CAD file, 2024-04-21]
hardware/footprint/ftsh-107-01-l-dv-k-a/FTSH-107-01-L-DV-K-A.step
8.89 x 6.98 x 5.84 mm
FTSH-107-01-L-DV-K-A_pins2
FTSH-107-01-L-DV-K-A_pins1
FTSH-107-01-L-DV-K-A_body

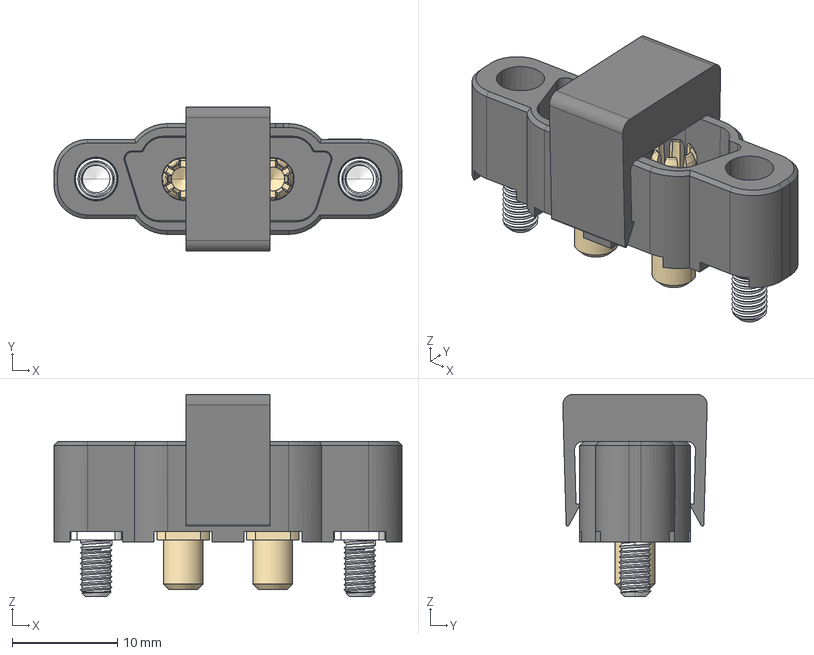
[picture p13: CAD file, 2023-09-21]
hardware/footprint/KA1-MV10205M1/KA1-MV10205M1.stp
33.0 x 13.7 x 19.2 mm
KA1-3110298
KA1-1100005 x 2
KA1-4220000 x 2
KA1-5050098A_AF2
KA1_LASER_H

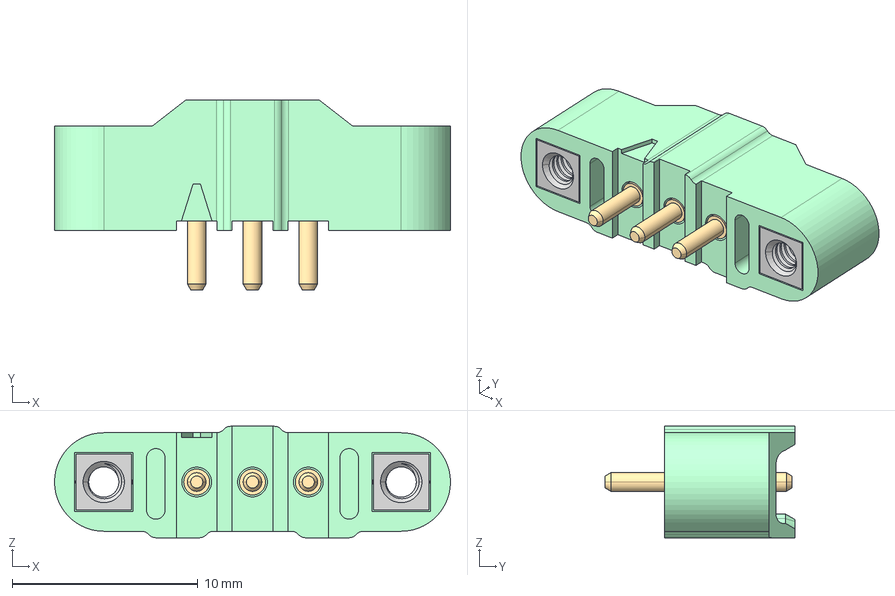
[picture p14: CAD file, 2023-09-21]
hardware/footprint/M300-MV10345M1/M300-MV10345M1.stp
21.3 x 10.2 x 6.00 mm
M300-322
M300-113 x 3
M80-210 x 2

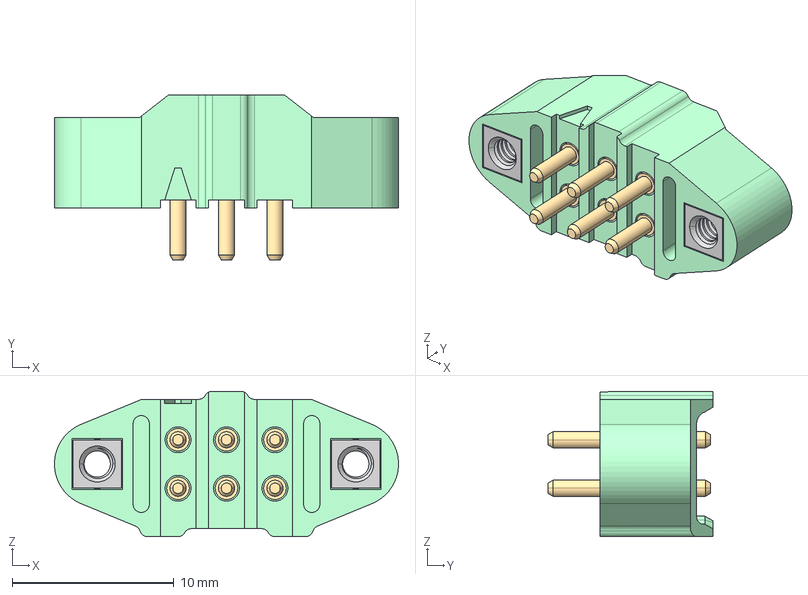
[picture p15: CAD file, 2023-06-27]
hardware/footprint/M300-MV30645M1/M300-MV30645M1.stp
21.3 x 10.2 x 9.00 mm
M300-321
M300-113 x 6
M80-210 x 2

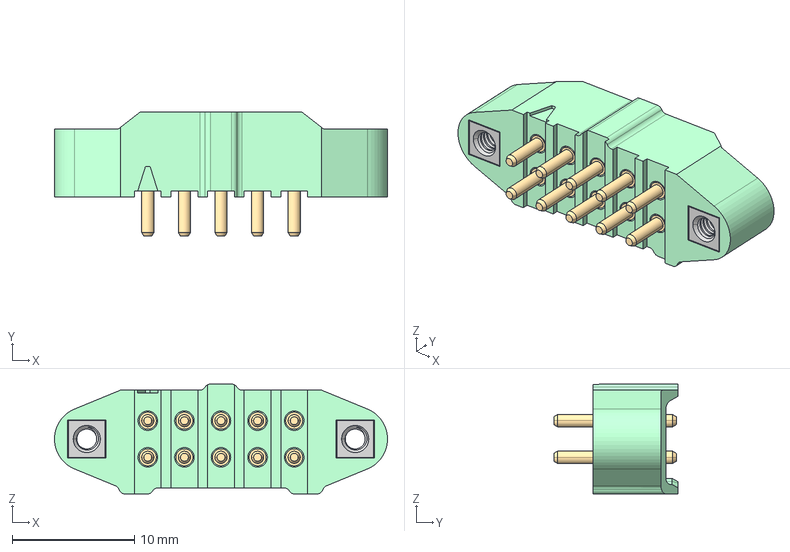
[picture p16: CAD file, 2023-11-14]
hardware/footprint/M300-MV3104M1/M300-MV31045M1.stp
27.3 x 10.2 x 9.00 mm
M300-3211096
M300-113 x 10
M80-210 x 2

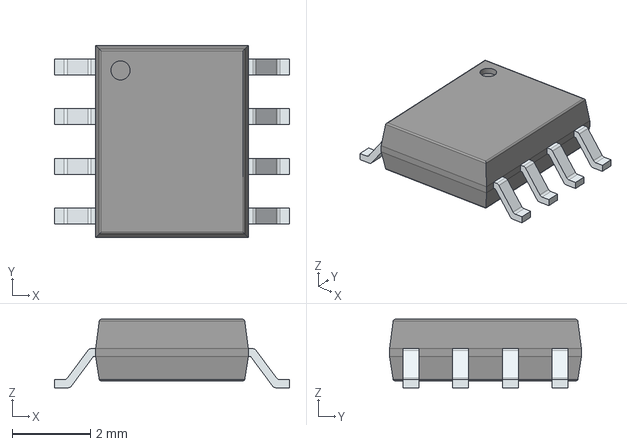
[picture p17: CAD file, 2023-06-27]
hardware/footprint/MCP1501-10E_SN/MCP1501-10E_SN.stp
6.00 x 4.90 x 1.75 mm
PinsArrayLR

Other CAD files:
hardware/footprint/MCP3561T-E_NC/MCP3561T-E_NC.stp
hardware/footprint/MCP3562T-E_NC/MCP3562T-E_NC.stp
hardware/footprint/PDSE1-S5-S5-D/PDSE1-S5-S5-D.step
hardware/footprint/PESE1-S5-S5-M-TR/PESE1-S5-S5-M-TR.stp
hardware/footprint/2920L500_24SLDR/2920L500_24SLDR.stp
hardware/footprint/ISO6763FDWR/ISO6763FDWR.stp
hardware/footprint/M80-5012622/M80-5012622.stp
hardware/footprint/M80-5100442/M80-5100442.stp
hardware/footprint/M80-5100622/M80-5100622.stp
hardware/footprint/M80-5101422/M80-5101422.stp
hardware/footprint/M80-5102022/M80-5102022.stp
hardware/footprint/M80-5301422/M80-5301422.stp
hardware/footprint/M80-5302042/M80-5302042.stp
hardware/footprint/M80-5302642/M80-5302642.stp
hardware/footprint/M80-5L10442MC/M80-5L10442MC.stp
hardware/footprint/M80-5L10642MC/M80-5L10642MC.stp
hardware/footprint/M80-5T10442MC/M80-5T10442MC.stp
hardware/footprint/M80-5T1062MC/M80-5T10642MC.stp
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

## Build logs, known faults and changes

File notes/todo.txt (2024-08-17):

high prio:
trzeba zmienić logikę latchowania
programowanie z zewnątrz 
zmienić limity max min
pomiar stacka od strony baterii

low prio:
soc:

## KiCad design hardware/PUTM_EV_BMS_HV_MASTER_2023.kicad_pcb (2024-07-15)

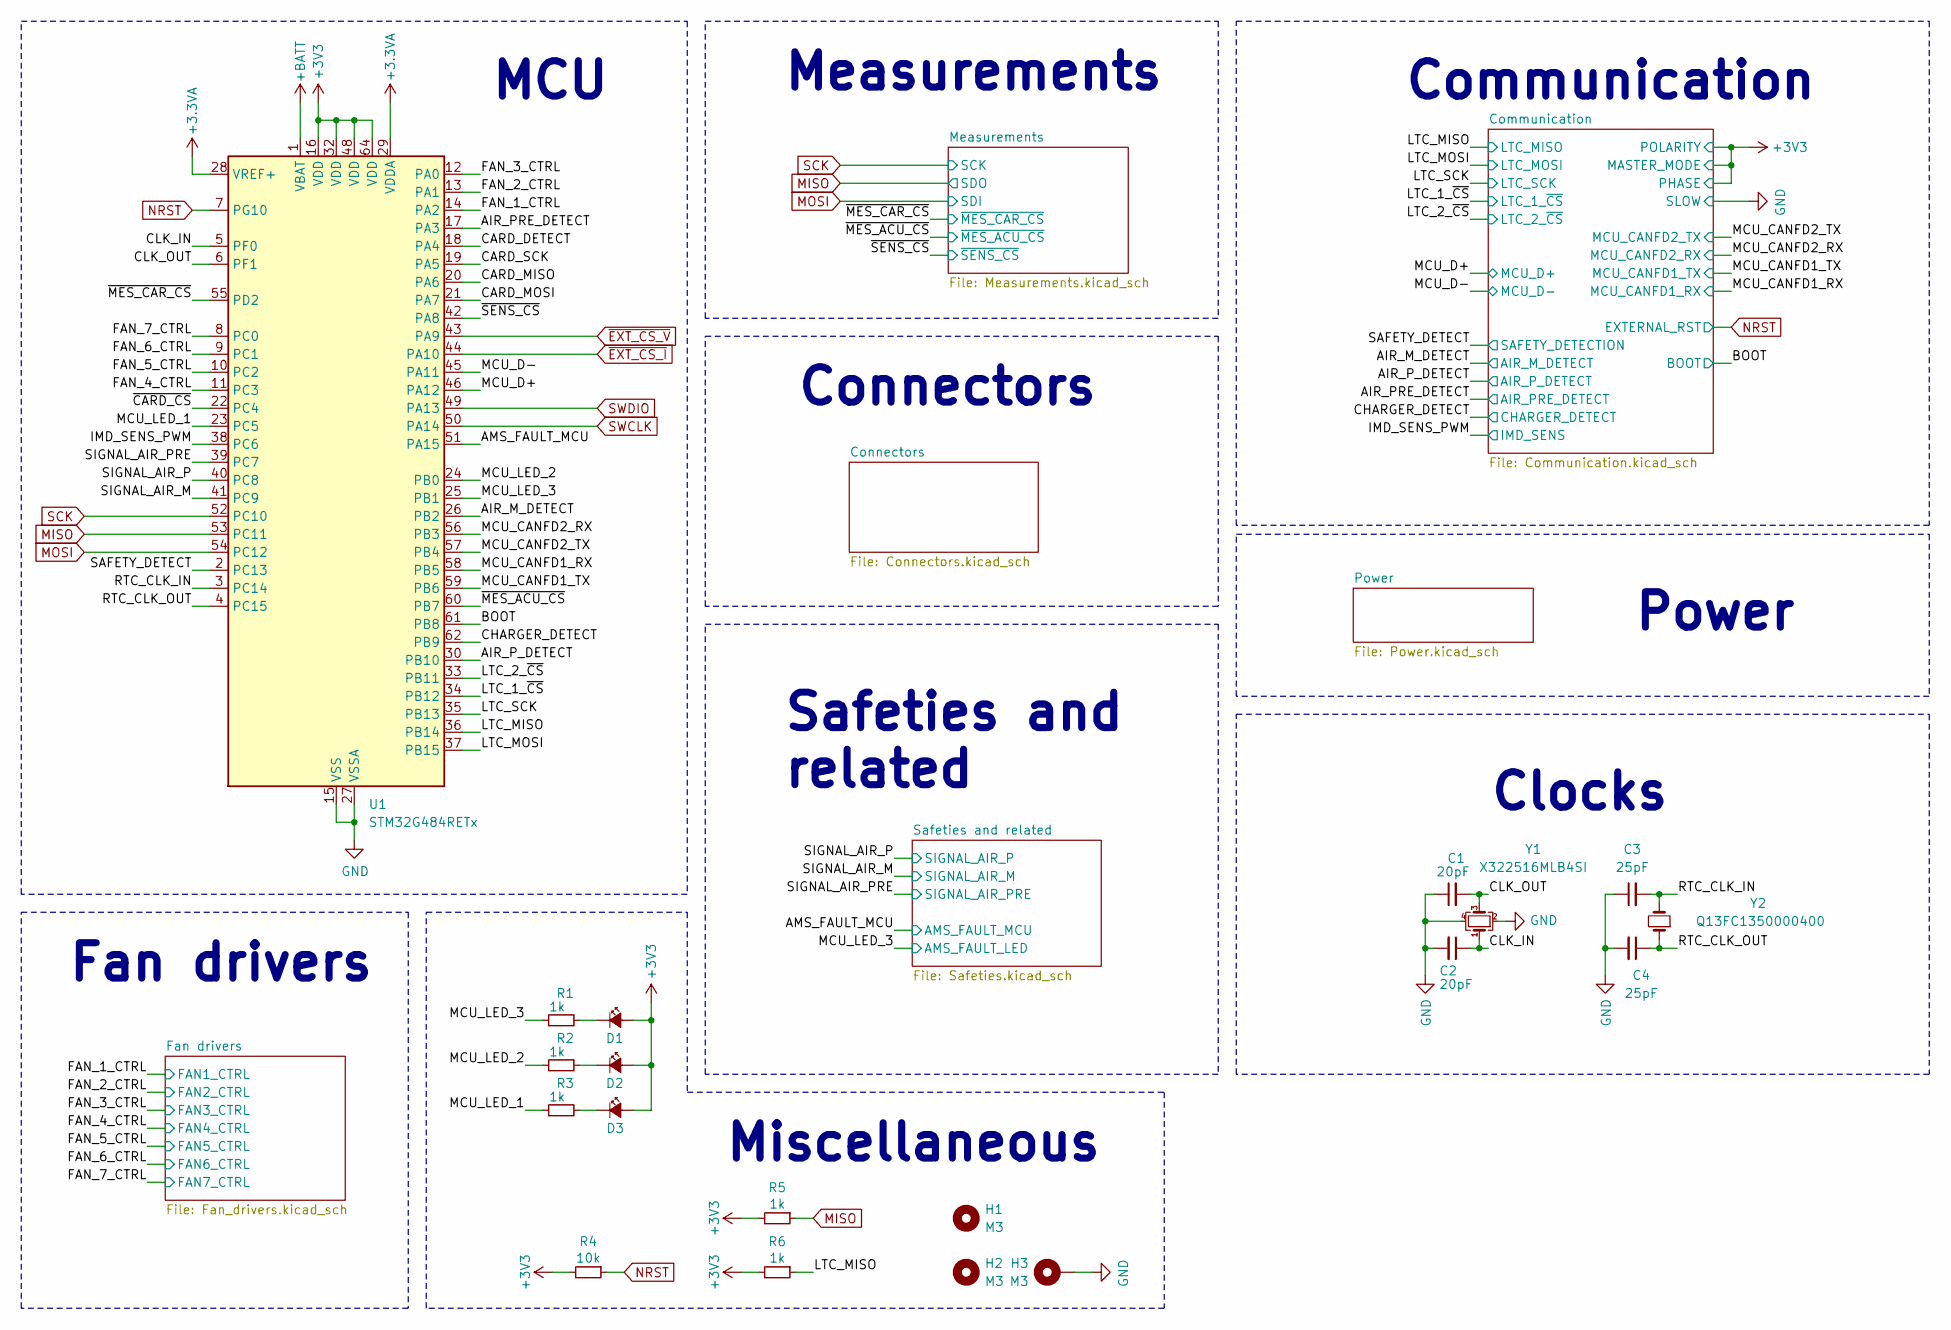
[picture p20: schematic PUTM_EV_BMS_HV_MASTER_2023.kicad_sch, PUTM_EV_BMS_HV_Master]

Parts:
C1, C2: 20pF; C_0603_1608Metric; Manufacturer_Part_Number --
C3, C4: 25pF; C_0603_1608Metric; Manufacturer_Part_Number 06035A250GAT2A; Mouser Part Number 581-06035A250GAT2A
D1, D2, D3: SML-D12U1WT86; LED_0603_1608Metric; Manufacturer_Part_Number --
H1, H2: M3; MountingHole_3.2mm_M3; Manufacturer_Part_Number --
H3: M3; MountingHole_3.2mm_M3_Pad_Via; Manufacturer_Part_Number --
R1, R2, R3, R5, R6: 1k; R_0603_1608Metric; Manufacturer_Part_Number --
R4: 10k; R_0603_1608Metric; Manufacturer_Part_Number --
U1: STM32G484RETx; LQFP-64_10x10mm_P0.5mm; Manufacturer_Part_Number STM32G484RET6; Mouser Part Number 511-STM32G484RET6
Y1: X322516MLB4SI; Crystal_SMD_3225-4Pin_3.2x2.5mm; Manufacturer_Part_Number --
Y2: Q13FC1350000400; Crystal_SMD_3215-2Pin_3.2x1.5mm; Manufacturer_Part_Number --

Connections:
+3.3VA: U1.28 (VREF+), U1.29 (VDDA); also elsewhere on the board
+3V3: D1.2 (A), D2.2 (A), D3.2 (A), R4.2, R5.2, R6.2, U1.16 (VDD), U1.32 (VDD), U1.48 (VDD), U1.64 (VDD); also elsewhere on the board
+BATT: U1.1 (VBAT)
/AIR_M_DETECT: U1.26 (PB2); also elsewhere on the board
/AIR_PRE_DETECT: U1.17 (PA3); also elsewhere on the board
/AIR_P_DETECT: U1.30 (PB10); also elsewhere on the board
/AMS_FAULT_MCU: U1.51 (PA15); also elsewhere on the board
/BOOT: U1.61 (PB8); also elsewhere on the board
/CARD_DETECT: U1.18 (PA4)
/CARD_MISO: U1.20 (PA6)
/CARD_MOSI: U1.21 (PA7)
/CARD_SCK: U1.19 (PA5)
/CHARGER_DETECT: U1.62 (PB9); also elsewhere on the board
/CLK_IN: C2.1, U1.5 (PF0), Y1.1
/CLK_OUT: C1.2, U1.6 (PF1), Y1.3
/FAN_1_CTRL: U1.14 (PA2); also elsewhere on the board
/FAN_2_CTRL: U1.13 (PA1); also elsewhere on the board
/FAN_3_CTRL: U1.12 (PA0); also elsewhere on the board
/FAN_4_CTRL: U1.11 (PC3); also elsewhere on the board
/FAN_5_CTRL: U1.10 (PC2); also elsewhere on the board
/FAN_6_CTRL: U1.9 (PC1); also elsewhere on the board
/FAN_7_CTRL: U1.8 (PC0); also elsewhere on the board
/IMD_SENS_PWM: U1.38 (PC6); also elsewhere on the board
/LTC_1_~CS: U1.34 (PB12); also elsewhere on the board
/LTC_2_~CS: U1.33 (PB11); also elsewhere on the board
/LTC_MISO: R6.1, U1.36 (PB14); also elsewhere on the board
/LTC_MOSI: U1.37 (PB15); also elsewhere on the board
/LTC_SCK: U1.35 (PB13); also elsewhere on the board
/MCU_CANFD1_RX: U1.58 (PB5); also elsewhere on the board
/MCU_CANFD1_TX: U1.59 (PB6); also elsewhere on the board
/MCU_CANFD2_RX: U1.56 (PB3); also elsewhere on the board
/MCU_CANFD2_TX: U1.57 (PB4); also elsewhere on the board
/MCU_D+: U1.46 (PA12); also elsewhere on the board
/MCU_D-: U1.45 (PA11); also elsewhere on the board
/MCU_LED_1: R3.1, U1.23 (PC5)
/MCU_LED_2: R2.1, U1.24 (PB0)
/MCU_LED_3: R1.1, U1.25 (PB1)
/RTC_CLK_IN: C3.2, U1.3 (PC14), Y2.2
/RTC_CLK_OUT: C4.1, U1.4 (PC15), Y2.1
/SAFETY_DETECT: U1.2 (PC13); also elsewhere on the board
/SIGNAL_AIR_M: U1.41 (PC9); also elsewhere on the board
/SIGNAL_AIR_P: U1.40 (PC8); also elsewhere on the board
/SIGNAL_AIR_PRE: U1.39 (PC7); also elsewhere on the board
/~CARD_CS: U1.22 (PC4)
/~MES_ACU_CS: U1.60 (PB7); also elsewhere on the board
/~MES_CAR_CS: U1.55 (PD2); also elsewhere on the board
/~SENS_CS: U1.42 (PA8); also elsewhere on the board
GND: C1.1, C2.2, C3.1, C4.2, H3.1, U1.15 (VSS), U1.27 (VSSA), U1.31 (VSS), U1.47 (VSS), U1.63 (VSS), Y1.2, Y1.4; also elsewhere on the board
MISO: R5.1, U1.53 (PC11); also elsewhere on the board
MOSI: U1.54 (PC12); also elsewhere on the board
NRST: R4.1, U1.7 (PG10); also elsewhere on the board
unnamed: D1.1 (K), R1.2
unnamed: D2.1 (K), R2.2
unnamed: D3.1 (K), R3.2
SCK: U1.52 (PC10); also elsewhere on the board
SWCLK: U1.50 (PA14); also elsewhere on the board
SWDIO: U1.49 (PA13); also elsewhere on the board
~EXT_CS_I: U1.44 (PA10); also elsewhere on the board
~EXT_CS_V: U1.43 (PA9); also elsewhere on the board

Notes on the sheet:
Power
Clocks
Communication
Connectors
MCU
Measurements
Miscellaneous
Safeties and related
Fan drivers

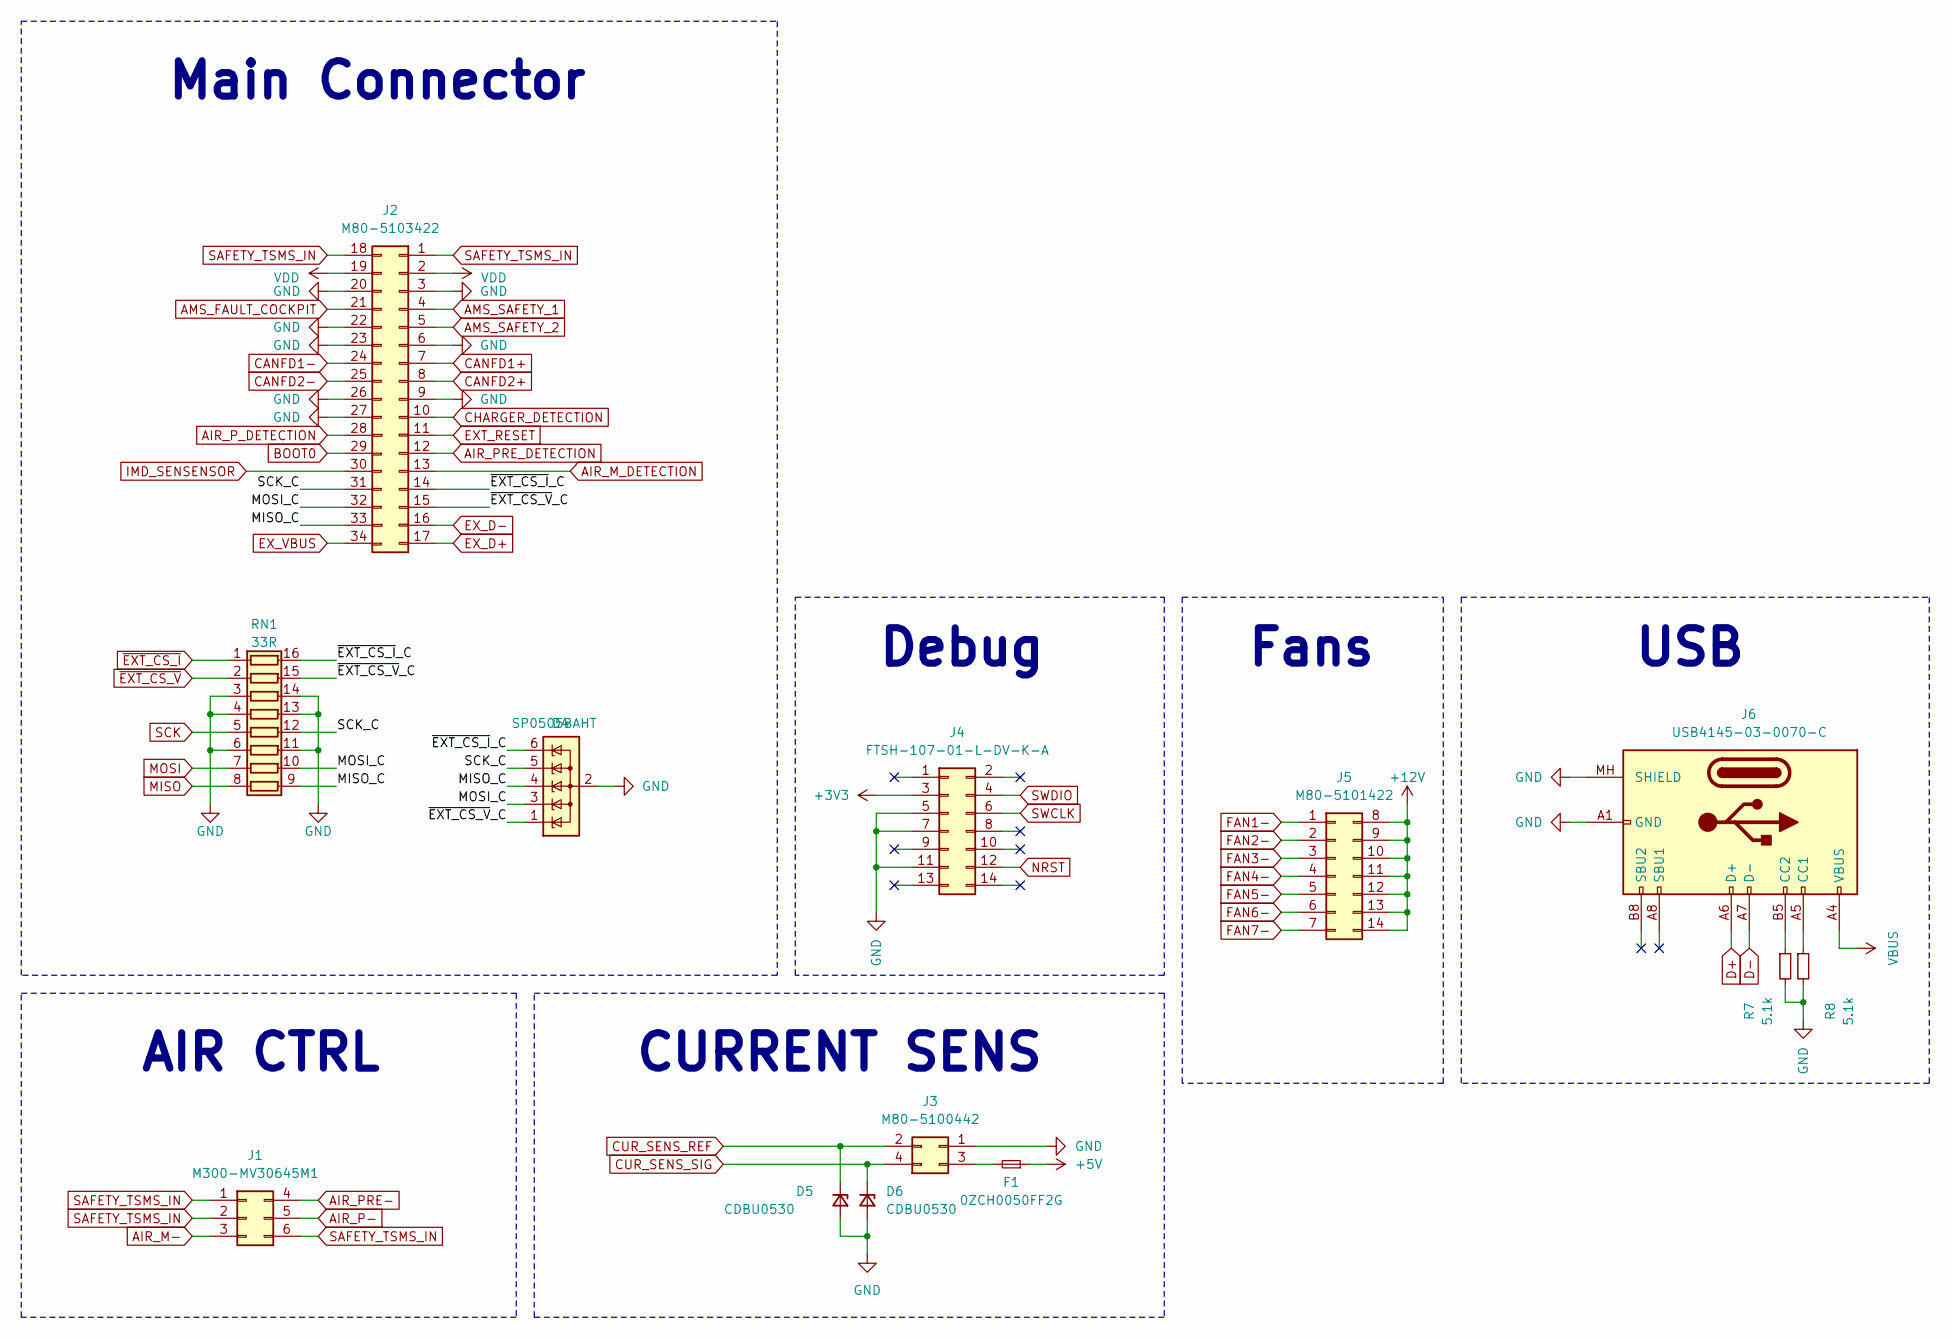
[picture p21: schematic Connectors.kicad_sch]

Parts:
D4: SP0505BAHT; SOT-23-6; Manufacturer_Part_Number SP0505BAHTG; Mouser Part Number 576-SP0505BAHTG
D5, D6: CDBU0530; D_0603_1608Metric; Manufacturer_Part_Number TSZU52C13 RGG; Mouser Part Number 821-TSZU52C13RGG
F1: 0ZCH0050FF2G; Fuse_1210_3225Metric; Manufacturer_Part_Number 0ZCH0050FF2G; Mouser Part Number 530-0ZCH0050FF2G
J1: M300-MV30645M1; M300MV30645M1; Mouser Part Number 855-M300-MV30645M1
J2: M80-5103422; M80-51034YY; Manufacturer_Part_Number M80-5103422; Mouser Part Number 855-M80-5103422
J3: M80-5100442; M80-51004YY; Mouser Part Number 855-M80-5100442
J4: FTSH-107-01-L-DV-K-A; FTSH-107-XX-YYY-DV-K-A; Mouser Part Number 200-FTSH10701LDVKA
J5: M80-5101422; M80-51014YY; Manufacturer_Part_Number M80-5101422; Mouser Part Number 855-M80-5101422
J6: USB4145-03-0070-C; USB4145030070C; Mouser Part Number 640-USB4145-3-0070-C
R7, R8: 5.1k; R_0603_1608Metric; Manufacturer_Part_Number --
RN1: 33R; R_Array_Convex_8x0602; Manufacturer_Part_Number 742C163470JP; Mouser Part Number 774-742C163470JP

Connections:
+3V3: J4.3; also elsewhere on the board
+5V: F1.1; also elsewhere on the board
+12V: J5.8, J5.9, J5.10, J5.11, J5.12, J5.13, J5.14; also elsewhere on the board
/Connectors/MISO_C: D4.4 (K), J2.33, RN1.9 (R8.2)
/Connectors/MOSI_C: D4.3 (K), J2.32, RN1.10 (R7.2)
/Connectors/SCK_C: D4.5 (K), J2.31, RN1.12 (R5.2)
/Connectors/~EXT_CS_I_C: D4.6 (K), J2.14, RN1.16 (R1.2)
/Connectors/~EXT_CS_V_C: D4.1 (K), J2.15, RN1.15 (R2.2)
AIR_M-: J1.3; also elsewhere on the board
AIR_M_DETECTION: J2.13; also elsewhere on the board
AIR_P-: J1.5; also elsewhere on the board
AIR_PRE-: J1.4; also elsewhere on the board
AIR_PRE_DETECTION: J2.12; also elsewhere on the board
AIR_P_DETECTION: J2.28; also elsewhere on the board
AMS_FAULT_COCKPIT: J2.21
AMS_SAFETY_1: J2.4; also elsewhere on the board
AMS_SAFETY_2: J2.5; also elsewhere on the board
BOOT0: J2.29; also elsewhere on the board
CANFD1+: J2.7; also elsewhere on the board
CANFD1-: J2.24; also elsewhere on the board
CANFD2+: J2.8; also elsewhere on the board
CANFD2-: J2.25; also elsewhere on the board
CHARGER_DETECTION: J2.10; also elsewhere on the board
CUR_SENS_REF: D5.1 (K), J3.2; also elsewhere on the board
CUR_SENS_SIG: D6.1 (K), J3.4; also elsewhere on the board
D+: J6.A6 (D+), J6.B6 (D+); also elsewhere on the board
D-: J6.A7 (D-), J6.B7 (D-); also elsewhere on the board
EXT_RESET: J2.11; also elsewhere on the board
EX_D+: J2.17; also elsewhere on the board
EX_D-: J2.16; also elsewhere on the board
EX_VBUS: J2.34; also elsewhere on the board
FAN1-: J5.1; also elsewhere on the board
FAN2-: J5.2; also elsewhere on the board
FAN3-: J5.3; also elsewhere on the board
FAN4-: J5.4; also elsewhere on the board
FAN5-: J5.5; also elsewhere on the board
FAN6-: J5.6; also elsewhere on the board
FAN7-: J5.7; also elsewhere on the board
GND: D4.2 (A), D5.2 (A), D6.2 (A), J2.3, J2.6, J2.9, J2.20, J2.22, J2.23, J2.26, J2.27, J3.1, J4.5, J4.7, J4.11, J6.A1 (GND), J6.A12 (GND), J6.B1 (GND), J6.B12 (GND), J6.MH (SHIELD), R7.2, R8.2, RN1.3 (R3.1), RN1.4 (R4.1), RN1.6 (R6.1), RN1.11 (R6.2), RN1.13 (R4.2), RN1.14 (R3.2); also elsewhere on the board
IMD_SENSENSOR: J2.30; also elsewhere on the board
MISO: RN1.8 (R8.1); also elsewhere on the board
MOSI: RN1.7 (R7.1); also elsewhere on the board
NRST: J4.12; also elsewhere on the board
unnamed: F1.2, J3.3
unnamed: J6.A5 (CC1), R8.1
unnamed: J6.B5 (CC2), R7.1
SAFETY_TSMS_IN: J1.1, J1.2, J1.6, J2.1, J2.18; also elsewhere on the board
SCK: RN1.5 (R5.1); also elsewhere on the board
SWCLK: J4.6; also elsewhere on the board
SWDIO: J4.4; also elsewhere on the board
VBUS: J6.A4 (VBUS), J6.A9 (VBUS), J6.B4 (VBUS), J6.B9 (VBUS); also elsewhere on the board
VDD: J2.2, J2.19; also elsewhere on the board
~EXT_CS_I: RN1.1 (R1.1); also elsewhere on the board
~EXT_CS_V: RN1.2 (R2.1); also elsewhere on the board

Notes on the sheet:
CURRENT SENS
Main Connector
USB
Fans
AIR CTRL
Debug

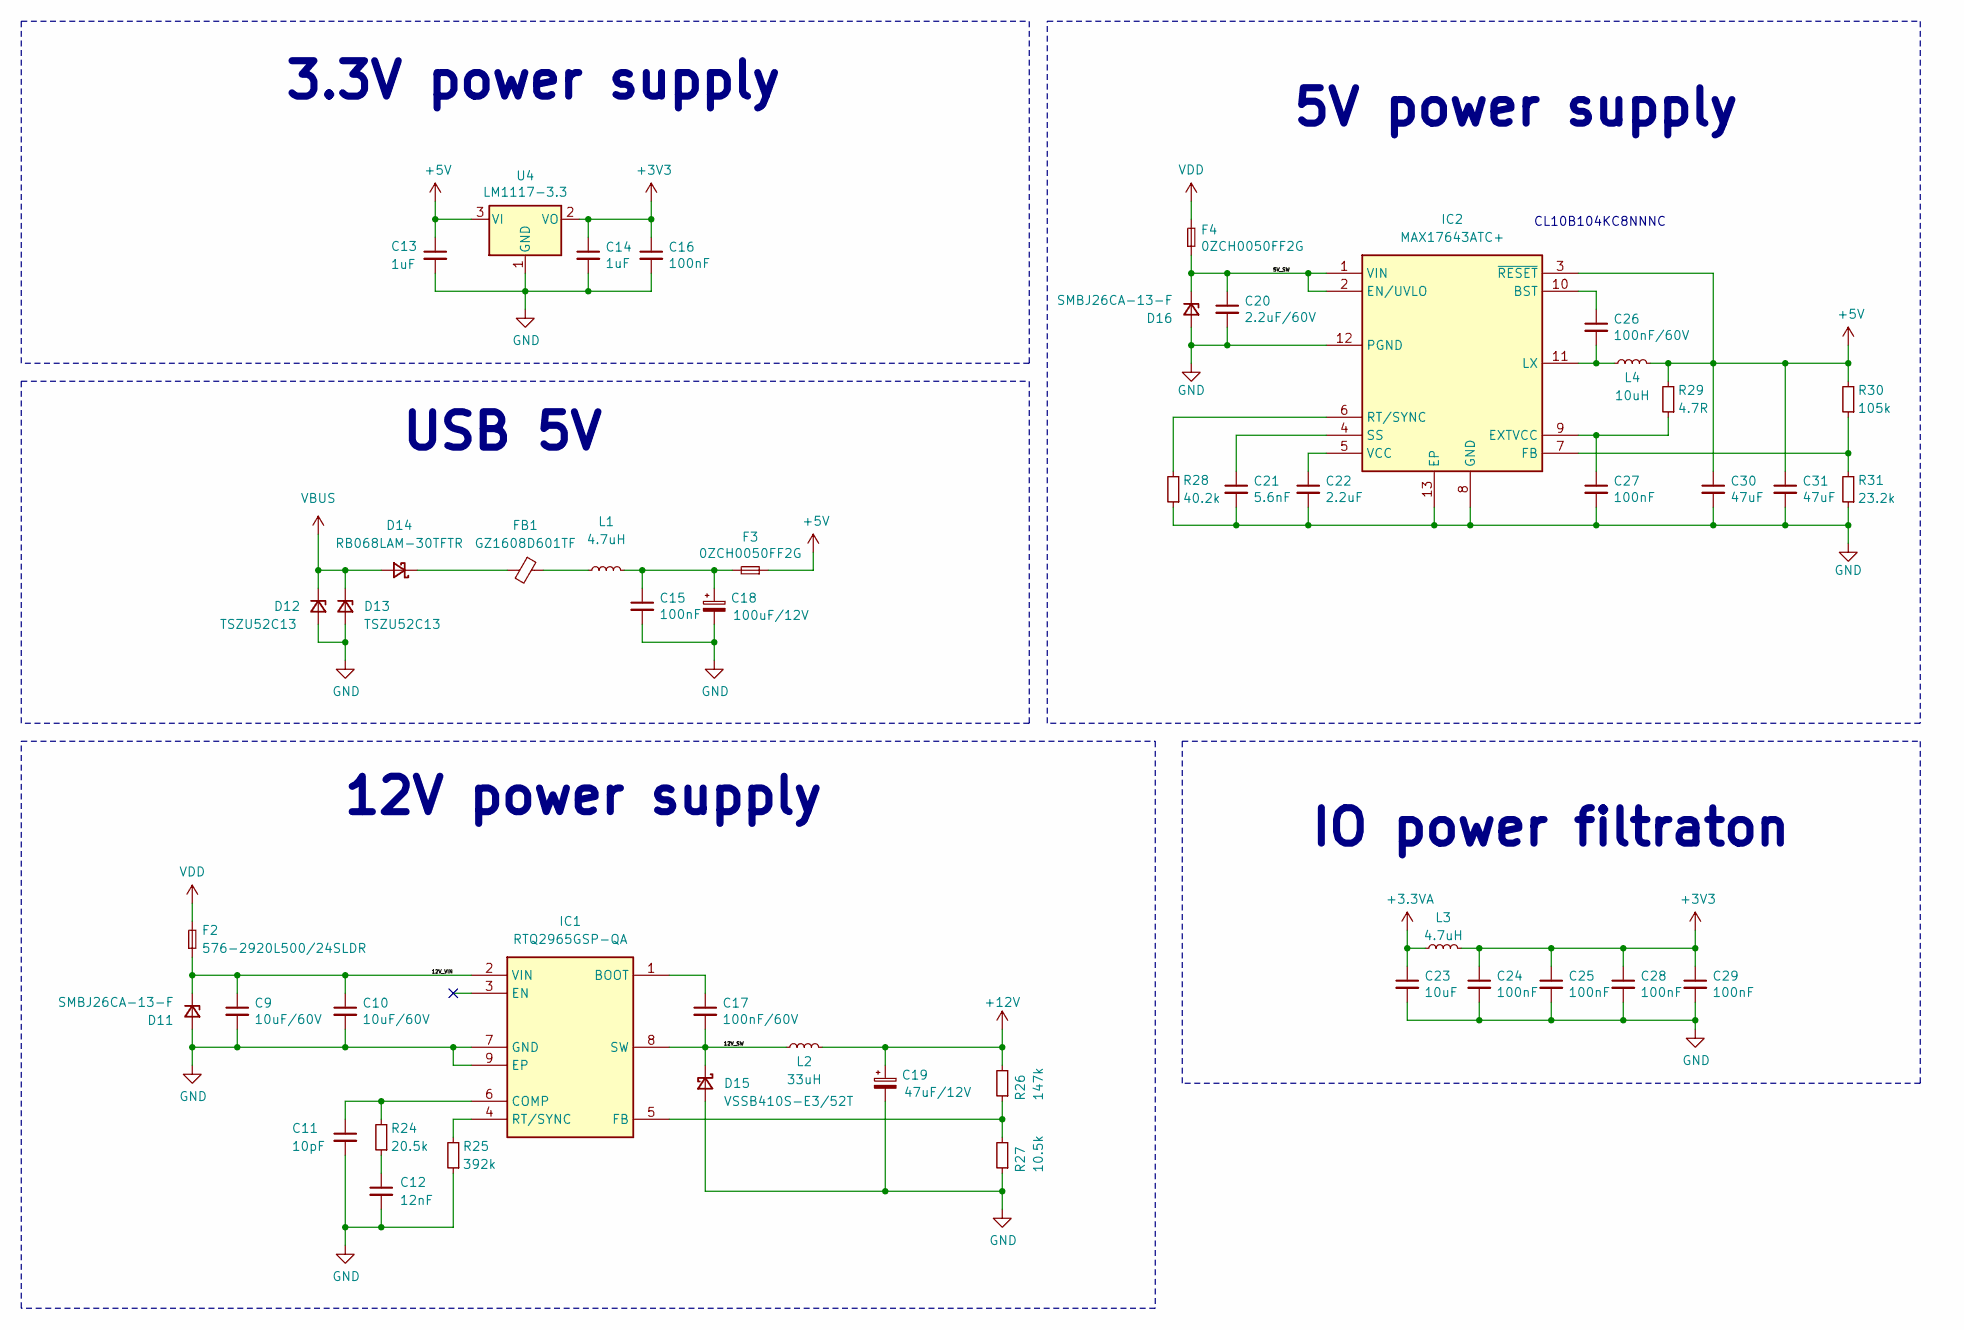
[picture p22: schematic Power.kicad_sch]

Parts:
C9, C10: 10uF/60V; C_1210_3225Metric; Manufacturer_Part_Number CGA6P1X7R1N106K250AC; Mouser Part Number 810-CGA6P1X7R1N106K2
C11: 10pF; C_0603_1608Metric; Manufacturer_Part_Number 06035A100JAT2A; Mouser Part Number 581-06035A100J
C12: 12nF; C_0603_1608Metric; Manufacturer_Part_Number CC0603KRX7R9BB123; Mouser Part Number 603-CC603KRX7R9BB123
C13, C14: 1uF; C_0603_1608Metric; Manufacturer_Part_Number C0603C105K8RACTU; Mouser Part Number 80-C0603C105K8R
C15, C16, C24, C25, C27, C28, C29: 100nF; C_0603_1608Metric; Manufacturer_Part_Number --
C17, C26: 100nF/60V; C_0603_1608Metric; Manufacturer_Part_Number CL10B104KC8NNNC; Mouser Part Number 187-CL10B104KC8NNNC
C18: 100uF/12V; CP_Elec_5x4.5; Manufacturer_Part_Number VZS101M1ATR-0506; Mouser Part Number 140-VZS101M1ATR0506
C19: 47uF/12V; CP_Elec_5x4.5; Manufacturer_Part_Number 865080342006; Mouser Part Number 710-865080342006
C20: 2.2uF/60V; C_1210_3225Metric; Manufacturer_Part_Number CL32B225KCJSNNE; Mouser Part Number 187-CL32B225KCJSNNE
C21: 5.6nF; C_0603_1608Metric; Manufacturer_Part_Number 06035C562KAT2A; Mouser Part Number 581-06035C562K
C22: 2.2uF; C_0603_1608Metric; Manufacturer_Part_Number CL10A225KO8NNWC; Mouser Part Number 187-CL10A225KO8NNWC
C23: 10uF; C_0603_1608Metric; Manufacturer_Part_Number --
C30, C31: 47uF; C_0603_1608Metric; Manufacturer_Part_Number CM105X5R476M06AT; Mouser Part Number 581-CM105X5R476M06AT
D11, D16: SMBJ26CA-13-F; D_SMB; Manufacturer_Part_Number SMBJ26CA-13-F; Mouser Part Number 621-SMBJ26CA-13-F
D12, D13: TSZU52C13; D_0603_1608Metric; Manufacturer_Part_Number TSZU52C13 RGG; Mouser Part Number 821-TSZU52C13RGG
D14: RB068LAM-30TFTR; D_SOD-128; Manufacturer_Part_Number RB068LAM-30TFTR; Mouser Part Number 755-RB068LAM-30TFTR
D15: VSSB410S-E3/52T; D_SMB; Manufacturer_Part_Number VSSB410S-E3/52T; Mouser Part Number 625-VSSB410S-E3/52T
F2: 576-2920L500/24SLDR; 2920L700SLPR; Mouser Part Number 576-2920L500/24SLDR
F3, F4: 0ZCH0050FF2G; Fuse_1210_3225Metric; Manufacturer_Part_Number 0ZCH0050FF2G; Mouser Part Number 530-0ZCH0050FF2G
FB1: GZ1608D601TF; L_0603_1608Metric; Manufacturer_Part_Number --
IC1: RTQ2965GSP-QA; SOIC127P600X175-9N; Mouser Part Number 835-RTQ2965GSP-QA
IC2: MAX17643ATC+; SON50P300X300X80-13N; Mouser Part Number 700-MAX17643ATC+
L1, L3: 4.7uH; L_1206_3216Metric; Manufacturer_Part_Number LQM31PN4R7M00L; Mouser Part Number 81-LQM31PN4R7M00L
L2: 33uH; L_Bourns_SRP1038C_10.0x10.0mm; Manufacturer_Part_Number SRP1038CC-330M; Mouser Part Number 652-SRP1038CC-330M
L4: 10uH; L_Coilcraft_XAL5050-XXX; Manufacturer_Part_Number XAL5050-103MEC; Mouser Part Number 994-XAL5050-103MEC
R24: 20.5k; R_0603_1608Metric; Manufacturer_Part_Number CRCW060320K5FKEA; Mouser Part Number 71-CRCW0603-20.5K-E3
R25: 392k; R_0603_1608Metric; Manufacturer_Part_Number AC0603FR-07392KL; Mouser Part Number 603-AC0603FR-07392KL
R26: 147k; R_0603_1608Metric; Manufacturer_Part_Number AC0603FR-07147KL; Mouser Part Number 603-AC0603FR-07147KL
R27: 10.5k; R_0603_1608Metric; Manufacturer_Part_Number CRCW060310K5FKEA; Mouser Part Number 71-CRCW0603-10.5K-E3
R28: 40.2k; R_0603_1608Metric; Manufacturer_Part_Number CRCW060340K2FKEB; Mouser Part Number 71-CRCW060340K2FKEB
R29: 4.7R; R_0603_1608Metric; Manufacturer_Part_Number CRCW06034R70FKEA; Mouser Part Number 71-CRCW06034R70FKEA
R30: 105k; R_0603_1608Metric; Manufacturer_Part_Number RT0603FRE07105KL; Mouser Part Number 603-RT0603FRE07105KL
R31: 23.2k; R_0603_1608Metric; Manufacturer_Part_Number RT0603FRE0723K2L; Mouser Part Number 603-RT0603FRE0723K2L
U4: LM1117-3.3; SOT-223-3_TabPin2; Manufacturer_Part_Number LM1117MP-3.3/NOPB; Mouser Part Number 926-LM1117MP-3.3NOPB

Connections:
+3.3VA: C23.1, L3.1; also elsewhere on the board
+3V3: C14.1, C16.1, C24.1, C25.1, C28.1, C29.1, L3.2, U4.2 (VO); also elsewhere on the board
+5V: C13.1, C30.1, C31.1, F3.1, IC2.3 (~RESET), L4.2, R29.2, R30.2, U4.3 (VI); also elsewhere on the board
+12V: C19.1, L2.2, R26.2; also elsewhere on the board
/Power/5V_SW: C20.1, D16.1 (K), F4.1, IC2.1 (VIN), IC2.2 (EN/UVLO)
/Power/12V_SW: C17.2, D15.1 (K), IC1.8 (SW), L2.1
/Power/12V_VIN: C9.1, C10.1, D11.1 (K), F2.1, IC1.2 (VIN)
GND: C9.2, C10.2, C11.2, C12.2, C13.2, C14.2, C15.2, C16.2, C18.2, C19.2, C20.2, C21.2, C22.2, C23.2, C24.2, C25.2, C27.2, C28.2, C29.2, C30.2, C31.2, D11.2 (A), D12.2 (A), D13.2 (A), D15.2 (A), D16.2 (A), IC1.7 (GND), IC1.9 (EP), IC2.8 (GND), IC2.12 (PGND), IC2.13 (EP), R25.1, R27.1, R28.1, R31.1, U4.1 (GND); also elsewhere on the board
unnamed: C12.1, R24.1
unnamed: C15.1, C18.1, F3.2, L1.2
unnamed: D14.1 (K), FB1.2
unnamed: FB1.1, L1.1
unnamed: C17.1, IC1.1 (BOOT)
unnamed: C11.1, IC1.6 (COMP), R24.2
unnamed: IC1.5 (FB), R26.1, R27.2
unnamed: IC1.4 (RT/SYNC), R25.2
unnamed: C26.1, IC2.10 (BST)
unnamed: C27.1, IC2.9 (EXTVCC), R29.1
unnamed: IC2.7 (FB), R30.1, R31.2
unnamed: C26.2, IC2.11 (LX), L4.1
unnamed: IC2.6 (RT/SYNC), R28.2
unnamed: C21.1, IC2.4 (SS)
unnamed: C22.1, IC2.5 (VCC)
VBUS: D12.1 (K), D13.1 (K), D14.2 (A); also elsewhere on the board
VDD: F2.2, F4.2; also elsewhere on the board

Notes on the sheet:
USB 5V
CL10B104KC8NNNC
3.3V power supply
IO power filtraton
12V power supply
5V power supply

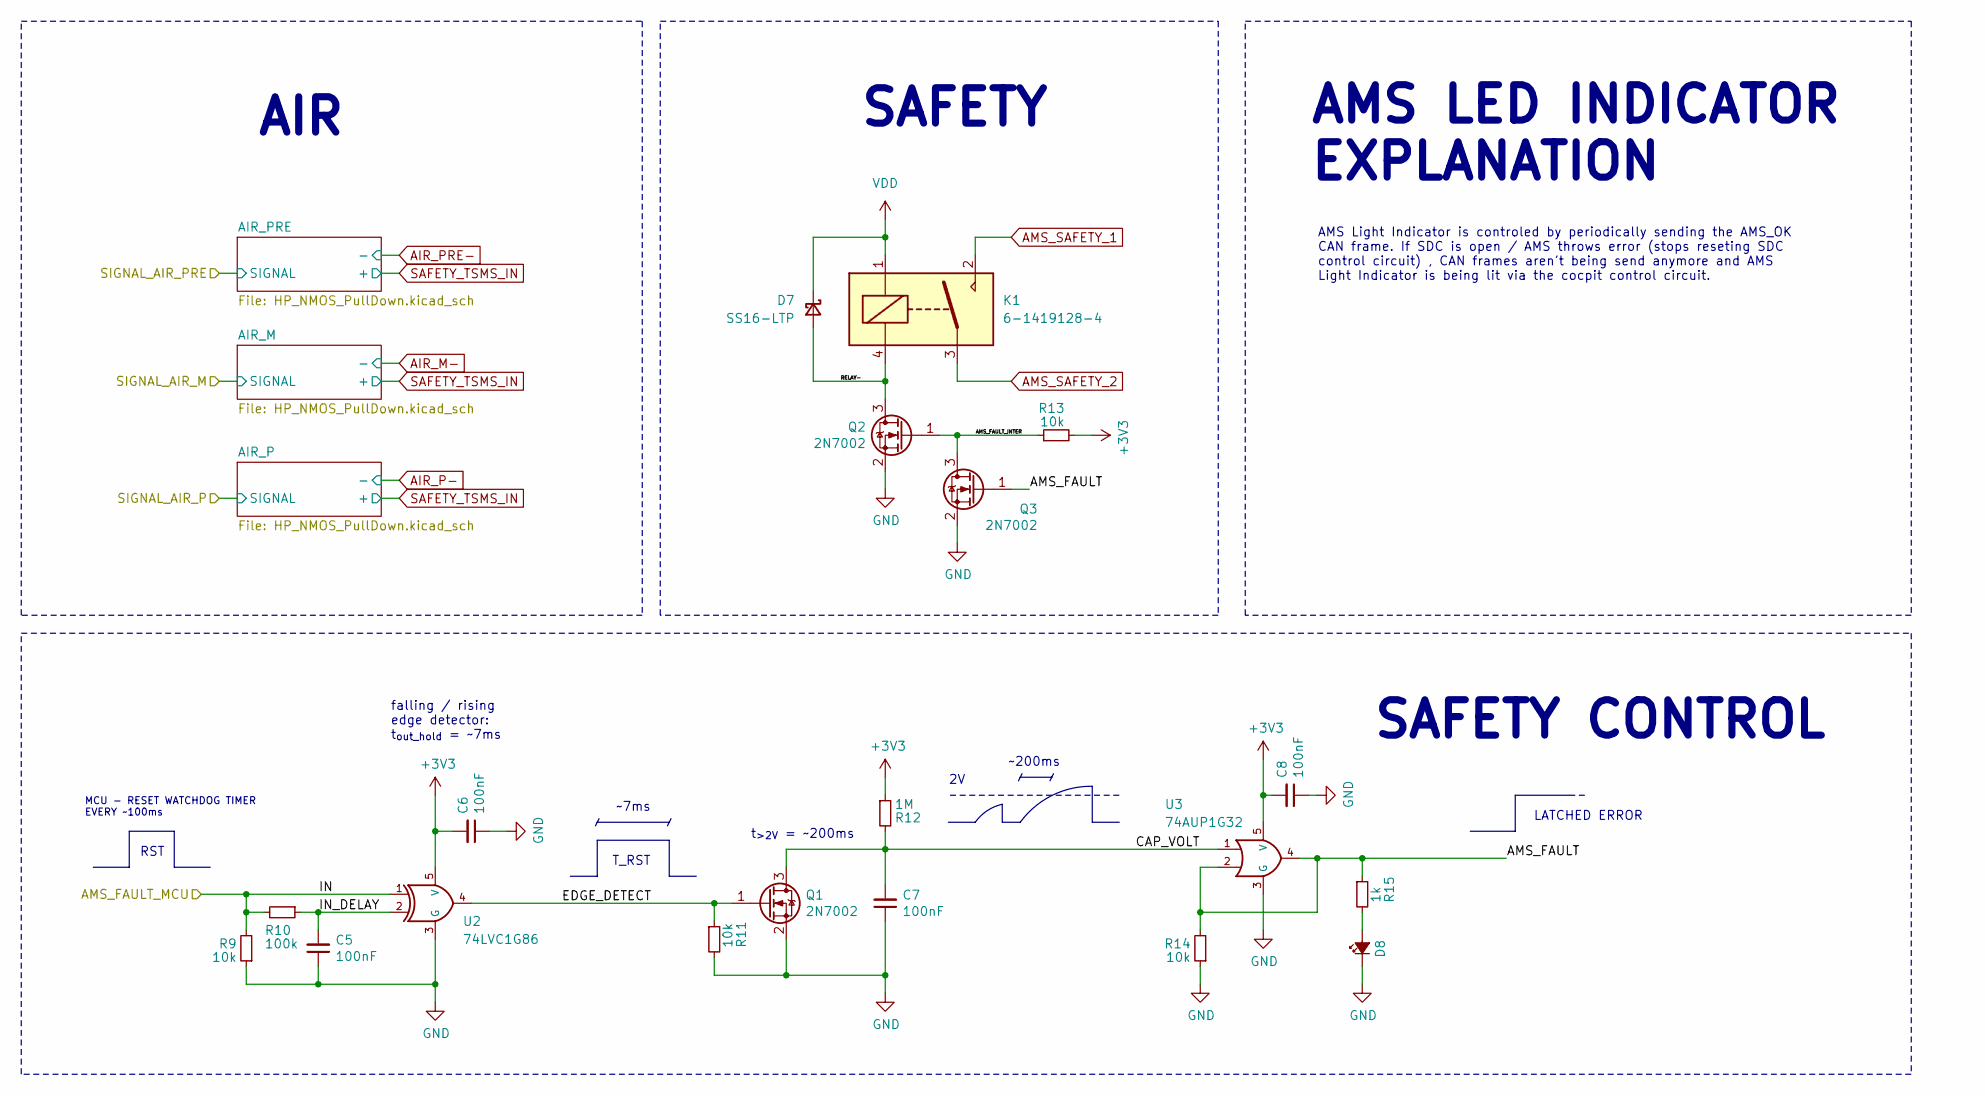
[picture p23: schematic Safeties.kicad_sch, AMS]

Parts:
C5, C6, C7, C8: 100nF; C_0603_1608Metric; Manufacturer_Part_Number --
D7: SS16-LTP; D_SMA; Manufacturer_Part_Number SS16-LTP; Mouser Part Number 833-SS16-LTP
D8: SML-D12U1WT86; LED_0603_1608Metric; Manufacturer_Part_Number --
K1: 6-1419128-4; 614191284; Mouser Part Number 655-6-1419128-4
Q1, Q2, Q3: 2N7002; SOT-23; Manufacturer_Part_Number --
R9, R11, R13, R14: 10k; R_0603_1608Metric; Manufacturer_Part_Number --
R10: 100k; R_0603_1608Metric; Manufacturer_Part_Number --
R12: 1M; R_0603_1608Metric; Manufacturer_Part_Number --
R15: 1k; R_0603_1608Metric; Manufacturer_Part_Number --
U2: 74LVC1G86; SOT-23-5_HandSoldering; Manufacturer_Part_Number SN74LVC1G86DBVR; Mouser Part Number 595-SN74LVC1G86DBVR
U3: 74AUP1G32; SOT-23-5_HandSoldering; Manufacturer_Part_Number SN74AUP1G32DBVR; Mouser Part Number 595-SN74AUP1G32DBVR

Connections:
+3V3: C6.2, C8.2, R12.1, R13.2, U2.5 (V), U3.5 (V); also elsewhere on the board
/AMS_FAULT_MCU: R9.2, R10.2, U2.1; also elsewhere on the board
/Safeties and related/AMS_FAULT: Q3.1 (G), R14.2, R15.1, U3.2, U3.4
/Safeties and related/AMS_FAULT_INTER: Q2.1 (G), Q3.3 (D), R13.1
/Safeties and related/CAP_VOLT: C7.2, Q1.3 (D), R12.2, U3.1
/Safeties and related/EDGE_DETECT: Q1.1 (G), R11.1, U2.4
/Safeties and related/IN_DELAY: C5.2, R10.1, U2.2
/Safeties and related/RELAY-: D7.2 (A), K1.4, Q2.3 (D)
AMS_SAFETY_1: K1.2; also elsewhere on the board
AMS_SAFETY_2: K1.3; also elsewhere on the board
GND: C5.1, C6.1, C7.1, C8.1, D8.1 (K), Q1.2 (S), Q2.2 (S), Q3.2 (S), R9.1, R11.2, R14.1, U2.3 (G), U3.3 (G); also elsewhere on the board
unnamed: D8.2 (A), R15.2
VDD: D7.1 (K), K1.1; also elsewhere on the board

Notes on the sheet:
AMS LED INDICATOR EXPLANATION
MCU - RESET WATCHDOG TIMER EVERY ~100ms
AIR
RST
T_RST
AMS Light Indicator is controled by periodically sending the AMS_OK CAN frame. If SDC is open / AMS throws error (stops reseting SDC control circuit) , CAN frames aren't being send anymore and AMS Light Indicator is being lit via the cocpit control circuit.
SAFETY CONTROL
~7ms
~200ms
LATCHED ERROR
t_{>2V} = ~200ms
falling / rising edge detector: t_{out_hold} = ~7ms
SAFETY

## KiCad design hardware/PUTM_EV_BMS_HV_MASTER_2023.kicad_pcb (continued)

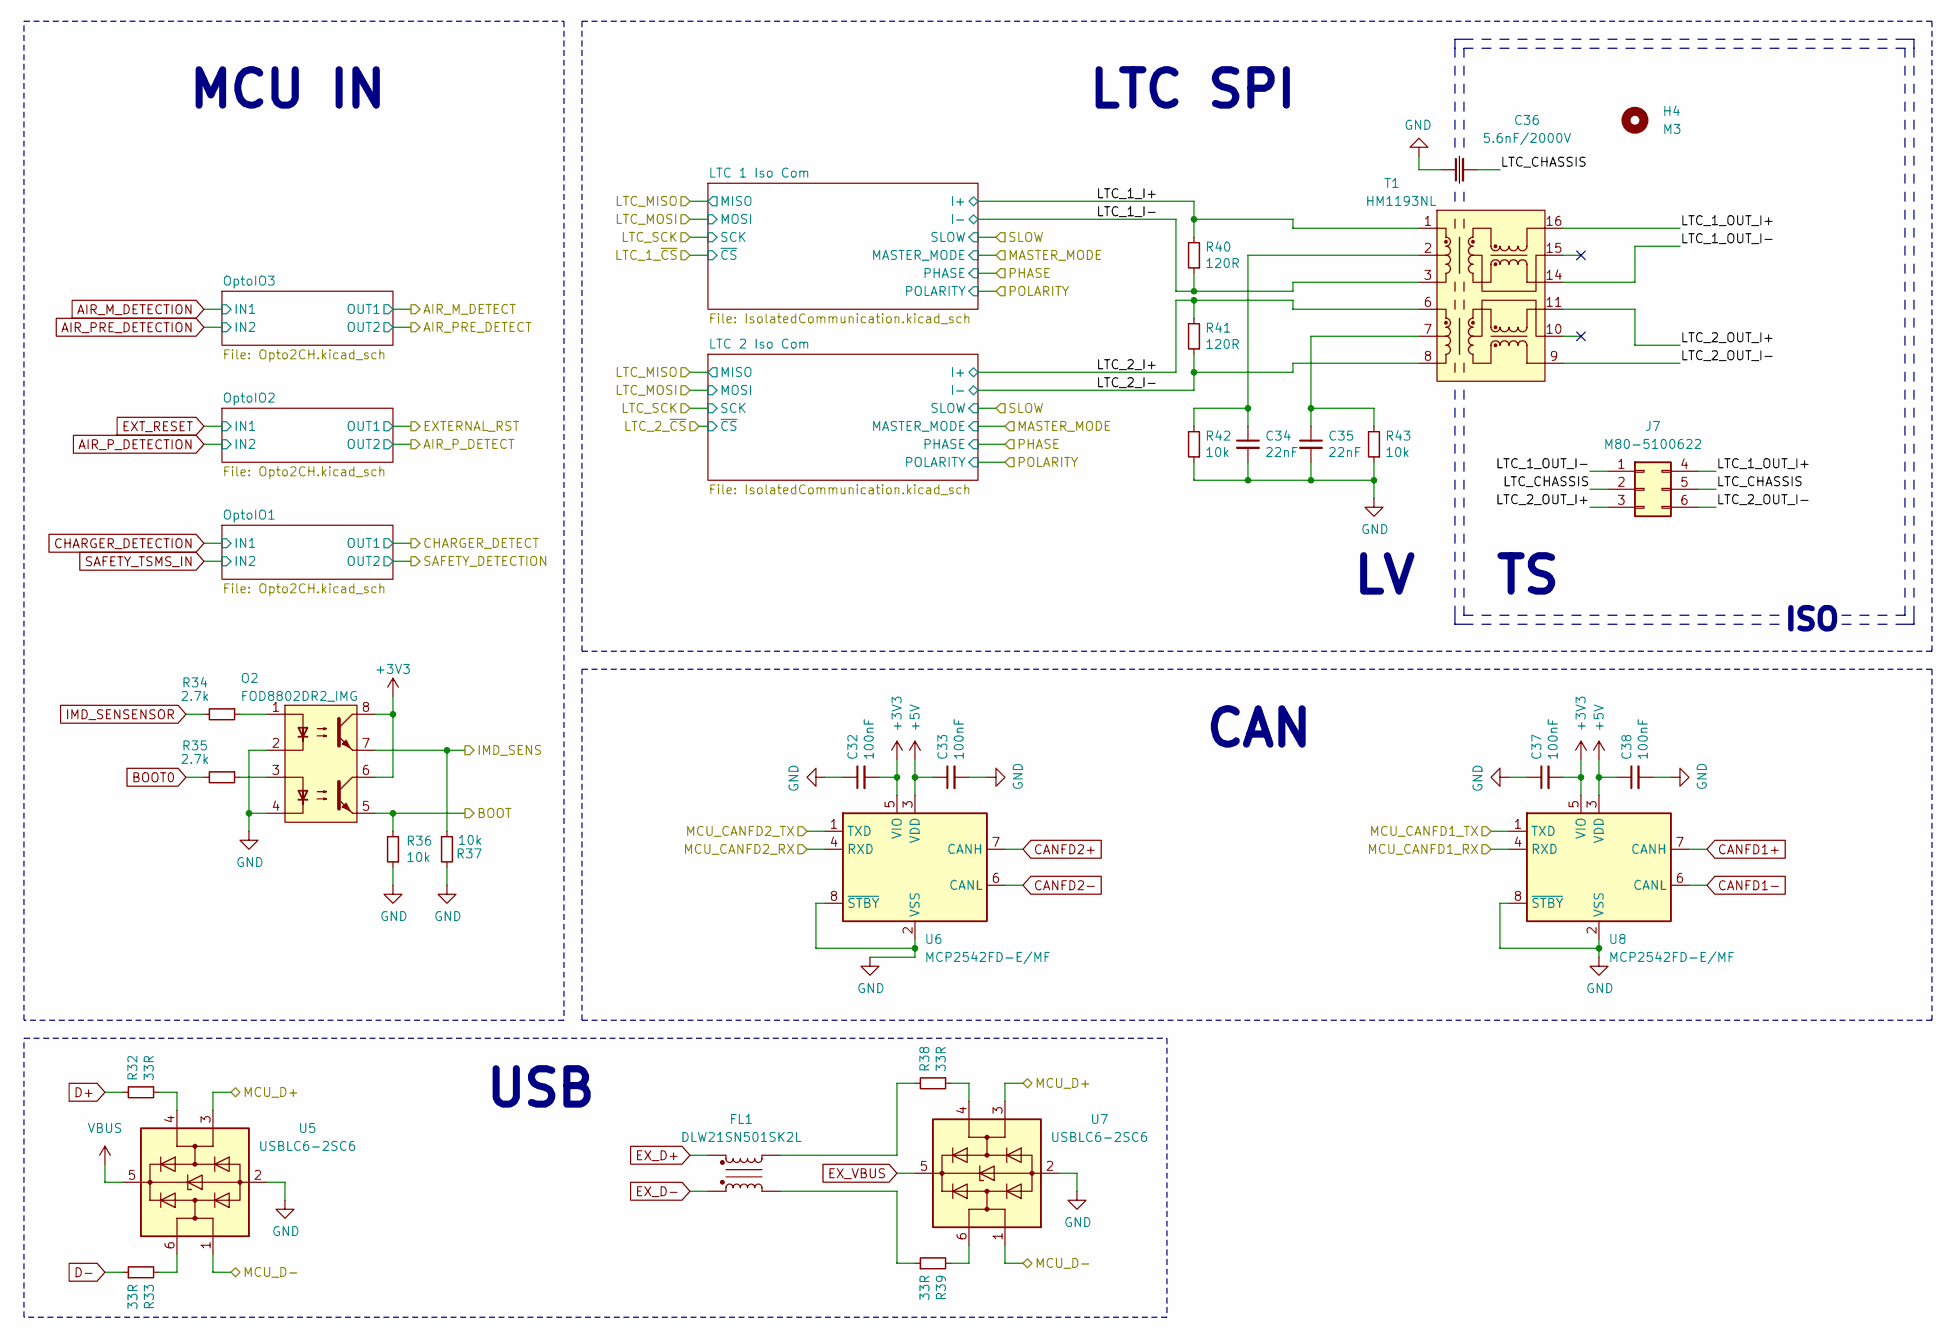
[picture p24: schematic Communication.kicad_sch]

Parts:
C32, C37: 100nF; C_0805_2012Metric; Manufacturer_Part_Number --
C33, C38: 100nF; C_0603_1608Metric; Manufacturer_Part_Number --
C34, C35: 22nF; C_0603_1608Metric; Manufacturer_Part_Number --
C36: 5.6nF/2000V; C2824; Mouser Part Number 80-C2824C562JGGAUTO
FL1: DLW21SN501SK2L; DLW21SN121HQ2L; Mouser Part Number 81-DLW21SN501SK2L
H4: M3; MountingHole_3.2mm_M3; Manufacturer_Part_Number --
J7: M80-5100622; M80-51006YY; Manufacturer_Part_Number M80-5100622; Mouser Part Number 855-M80-5100622
O2: FOD8802DR2_IMG; SOIC127P600X175-8N; Manufacturer_Part_Number FOD8802DR2; Mouser Part Number 863-FOD8802DR2
R32, R33, R38, R39: 33R; R_0603_1608Metric; Manufacturer_Part_Number --
R34, R35: 2.7k; R_0603_1608Metric; Manufacturer_Part_Number --
R36, R37, R42, R43: 10k; R_0603_1608Metric; Manufacturer_Part_Number --
R40, R41: 120R; R_0603_1608Metric; Manufacturer_Part_Number --
T1: HM1193NL; Transformer_Pulse_H1100NL; Manufacturer_Part_Number HM1193NL; Mouser Part Number 673-HM1193NL
U5, U7: USBLC6-2SC6; SOT-23-6; Manufacturer_Part_Number USBLC6-2SC6; Mouser Part Number 511-USBLC6-2SC6
U6, U8: MCP2542FD-E/MF; DFN-8-1EP_3x3mm_P0.65mm_EP1.55x2.4mm; Manufacturer_Part_Number MCP2542FD-E/MF; Mouser Part Number 579-MCP2542FD-E/MF

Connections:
+3V3: C32.2, C37.2, O2.6, O2.8, U6.5 (VIO), U8.5 (VIO); also elsewhere on the board
+5V: C33.1, C38.1, U6.3 (VDD), U8.3 (VDD); also elsewhere on the board
/BOOT: O2.5, R36.2; also elsewhere on the board
/Communication/LTC_1_I+: R40.2, T1.1; also elsewhere on the board
/Communication/LTC_1_I-: R40.1, T1.3; also elsewhere on the board
/Communication/LTC_1_OUT_I+: J7.4, T1.16
/Communication/LTC_1_OUT_I-: J7.1, T1.14
/Communication/LTC_2_I+: R41.2, T1.6; also elsewhere on the board
/Communication/LTC_2_I-: R41.1, T1.8; also elsewhere on the board
/Communication/LTC_2_OUT_I+: J7.3, T1.11
/Communication/LTC_2_OUT_I-: J7.6, T1.9
/Communication/LTC_CHASSIS: C36.2, J7.2, J7.5
/IMD_SENS_PWM: O2.7, R37.1; also elsewhere on the board
/MCU_CANFD1_RX: U8.4 (RXD); also elsewhere on the board
/MCU_CANFD1_TX: U8.1 (TXD); also elsewhere on the board
/MCU_CANFD2_RX: U6.4 (RXD); also elsewhere on the board
/MCU_CANFD2_TX: U6.1 (TXD); also elsewhere on the board
/MCU_D+: U5.3 (I/O2), U7.3 (I/O2); also elsewhere on the board
/MCU_D-: U5.1 (I/O1), U7.1 (I/O1); also elsewhere on the board
BOOT0: R35.2; also elsewhere on the board
CANFD1+: U8.7 (CANH); also elsewhere on the board
CANFD1-: U8.6 (CANL); also elsewhere on the board
CANFD2+: U6.7 (CANH); also elsewhere on the board
CANFD2-: U6.6 (CANL); also elsewhere on the board
D+: R32.2; also elsewhere on the board
D-: R33.1; also elsewhere on the board
EX_D+: FL1.4; also elsewhere on the board
EX_D-: FL1.1; also elsewhere on the board
EX_VBUS: U7.5 (VBUS); also elsewhere on the board
GND: C32.1, C33.2, C34.2, C35.2, C36.1, C37.1, C38.2, O2.2, O2.4, R36.1, R37.2, R42.1, R43.1, U5.2 (GND), U6.2 (VSS), U6.8 (~STBY), U6.9 (VSS), U7.2 (GND), U8.2 (VSS), U8.8 (~STBY), U8.9 (VSS); also elsewhere on the board
IMD_SENSENSOR: R34.2; also elsewhere on the board
unnamed: C34.1, R42.2, T1.2
unnamed: C35.1, R43.2, T1.7
unnamed: FL1.2, R39.1
unnamed: FL1.3, R38.2
unnamed: O2.1, R34.1
unnamed: O2.3, R35.1
unnamed: R32.1, U5.4 (I/O2)
unnamed: R33.2, U5.6 (I/O1)
unnamed: R38.1, U7.4 (I/O2)
unnamed: R39.2, U7.6 (I/O1)
VBUS: U5.5 (VBUS); also elsewhere on the board

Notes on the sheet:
LTC SPI
MCU IN
USB
ISO
CAN

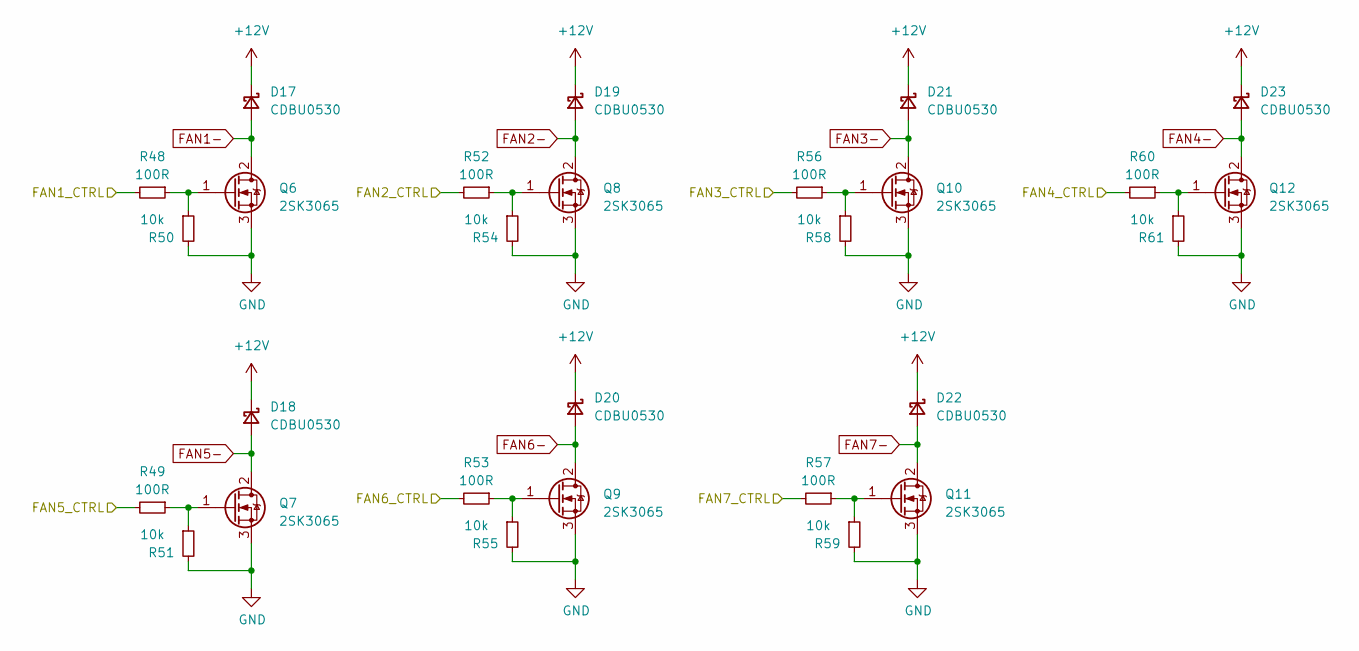
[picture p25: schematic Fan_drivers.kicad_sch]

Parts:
D17, D18, D19, D20, D21, D22, D23: CDBU0530; D_0603_1608Metric; Manufacturer_Part_Number CDBU0530; Mouser Part Number 750-CDBU0530
Q6, Q7, Q8, Q9, Q10, Q11, Q12: 2SK3065; SOT-89-3; Manufacturer_Part_Number 2SK3065T100; Mouser Part Number 755-2SK3065T100
R48, R49, R52, R53, R56, R57, R60: 100R; R_0603_1608Metric; Manufacturer_Part_Number --
R50, R51, R54, R55, R58, R59, R61: 10k; R_0603_1608Metric; Manufacturer_Part_Number --

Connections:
+12V: D17.1 (K), D18.1 (K), D19.1 (K), D20.1 (K), D21.1 (K), D22.1 (K), D23.1 (K); also elsewhere on the board
/FAN_1_CTRL: R48.2; also elsewhere on the board
/FAN_2_CTRL: R52.2; also elsewhere on the board
/FAN_3_CTRL: R56.2; also elsewhere on the board
/FAN_4_CTRL: R60.2; also elsewhere on the board
/FAN_5_CTRL: R49.2; also elsewhere on the board
/FAN_6_CTRL: R53.2; also elsewhere on the board
/FAN_7_CTRL: R57.2; also elsewhere on the board
FAN1-: D17.2 (A), Q6.2 (D); also elsewhere on the board
FAN2-: D19.2 (A), Q8.2 (D); also elsewhere on the board
FAN3-: D21.2 (A), Q10.2 (D); also elsewhere on the board
FAN4-: D23.2 (A), Q12.2 (D); also elsewhere on the board
FAN5-: D18.2 (A), Q7.2 (D); also elsewhere on the board
FAN6-: D20.2 (A), Q9.2 (D); also elsewhere on the board
FAN7-: D22.2 (A), Q11.2 (D); also elsewhere on the board
GND: Q6.3 (S), Q7.3 (S), Q8.3 (S), Q9.3 (S), Q10.3 (S), Q11.3 (S), Q12.3 (S), R50.2, R51.2, R54.2, R55.2, R58.2, R59.2, R61.2; also elsewhere on the board
unnamed: Q6.1 (G), R48.1, R50.1
unnamed: Q7.1 (G), R49.1, R51.1
unnamed: Q8.1 (G), R52.1, R54.1
unnamed: Q9.1 (G), R53.1, R55.1
unnamed: Q10.1 (G), R56.1, R58.1
unnamed: Q11.1 (G), R57.1, R59.1
unnamed: Q12.1 (G), R60.1, R61.1

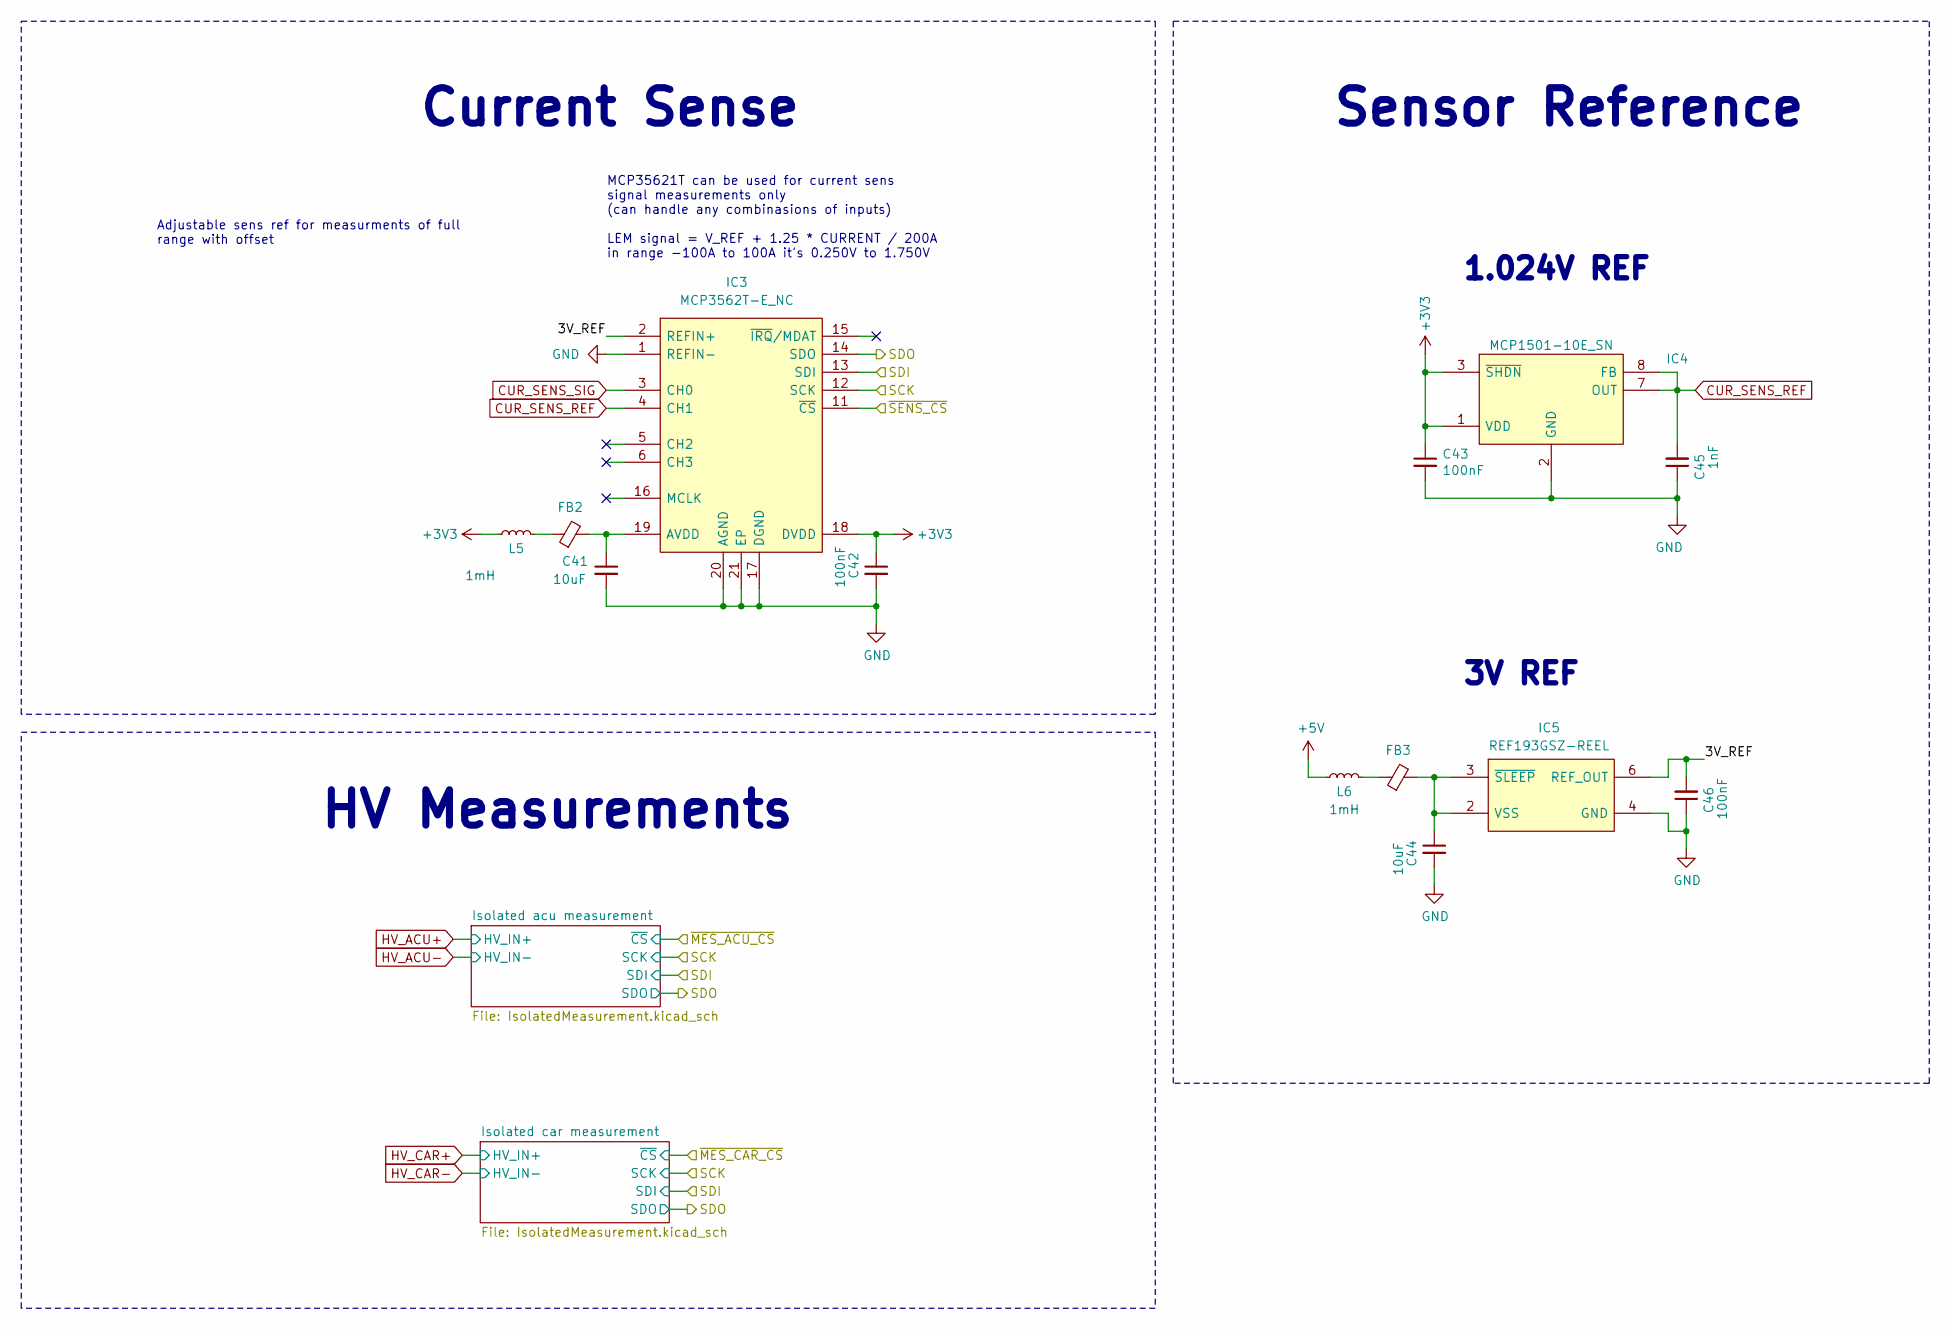
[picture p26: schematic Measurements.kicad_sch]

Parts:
C41, C44: 10uF; C_0603_1608Metric; Manufacturer_Part_Number --
C42, C43, C46: 100nF; C_0603_1608Metric; Manufacturer_Part_Number --
C45: 1nF; C_0603_1608Metric; Manufacturer_Part_Number --
FB2, FB3: GZ1608D601TF; L_0603_1608Metric; Manufacturer_Part_Number --
IC3: MCP3562T-E_NC; QFN40P300X300X60-21N-D; Mouser Part Number 579-MCP3562T-E/NC
IC4: MCP1501-10E_SN; SOIC127P600X175-8N; Mouser Part Number 579-MCP1501-10E/SN
IC5: REF193GSZ-REEL; SOIC127P600X175-8N; Mouser Part Number 584-REF196GSZ-R
L5, L6: 1mH; L_1206_3216Metric; Manufacturer_Part_Number LB3218T102K; Mouser Part Number 963-LB3218T102K

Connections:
+3V3: C42.1, C43.1, IC3.18 (DVDD), IC4.1 (VDD), IC4.3 (~SHDN), L5.1; also elsewhere on the board
+5V: L6.1; also elsewhere on the board
/Measurements/3V_REF: C46.2, IC3.2 (REFIN+), IC5.6 (REF_OUT)
/~SENS_CS: IC3.11 (~CS); also elsewhere on the board
CUR_SENS_REF: C45.2, IC3.4 (CH1), IC4.7 (OUT), IC4.8 (FB); also elsewhere on the board
CUR_SENS_SIG: IC3.3 (CH0); also elsewhere on the board
GND: C41.2, C42.2, C43.2, C44.2, C45.1, C46.1, IC3.1 (REFIN-), IC3.17 (DGND), IC3.20 (AGND), IC3.21 (EP), IC4.2 (GND), IC4.4 (GND), IC4.5 (GND), IC4.6 (GND), IC5.4 (GND); also elsewhere on the board
MISO: IC3.14 (SDO); also elsewhere on the board
MOSI: IC3.13 (SDI); also elsewhere on the board
unnamed: FB2.1, L5.2
unnamed: FB3.1, L6.2
unnamed: C41.1, FB2.2, IC3.19 (AVDD)
unnamed: C44.1, FB3.2, IC5.2 (VSS), IC5.3 (~SLEEP)
SCK: IC3.12 (SCK); also elsewhere on the board

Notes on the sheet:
HV Measurements
Adjustable sens ref for measurments of full range with offset
Sensor Reference
MCP35621T can be used for current sens signal measurements only (can handle any combinasions of inputs) LEM signal = V_REF + 1.25 * CURRENT / 200A in range -100A to 100A it's 0.250V to 1.750V
Current Sense
3V REF
1.024V REF

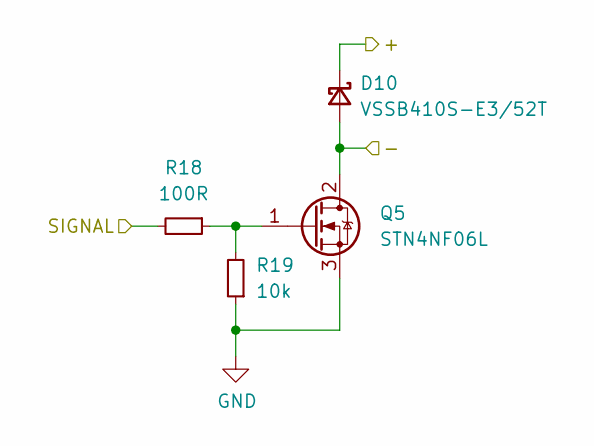
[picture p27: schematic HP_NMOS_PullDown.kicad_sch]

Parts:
D10: VSSB410S-E3/52T; D_SMB; Manufacturer_Part_Number VSSB410S-E3/52T; Mouser Part Number 625-VSSB410S-E3/52T
Q5: STN4NF06L; SOT-223-3_TabPin2; Manufacturer_Part_Number IRLL024ZTRPBF; Mouser Part Number 942-IRLL024ZTRPBF
R18: 100R; R_0603_1608Metric; Manufacturer_Part_Number --
R19: 10k; R_0603_1608Metric; Manufacturer_Part_Number --

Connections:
/SIGNAL_AIR_PRE: R18.2; also elsewhere on the board
AIR_PRE-: D10.2 (A), Q5.2 (D); also elsewhere on the board
GND: Q5.3 (S), R19.1; also elsewhere on the board
unnamed: Q5.1 (G), R18.1, R19.2
SAFETY_TSMS_IN: D10.1 (K); also elsewhere on the board

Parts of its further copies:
D9, D24: VSSB410S-E3/52T; D_SMB; Manufacturer_Part_Number VSSB410S-E3/52T; Mouser Part Number 625-VSSB410S-E3/52T
Q4, Q13: STN4NF06L; SOT-223-3_TabPin2; Manufacturer_Part_Number IRLL024ZTRPBF; Mouser Part Number 942-IRLL024ZTRPBF
R16, R66: 100R; R_0603_1608Metric; Manufacturer_Part_Number --
R17, R67: 10k; R_0603_1608Metric; Manufacturer_Part_Number --

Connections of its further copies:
/SIGNAL_AIR_M: R16.2; also elsewhere on the board
/SIGNAL_AIR_P: R66.2; also elsewhere on the board
AIR_M-: D9.2 (A), Q4.2 (D); also elsewhere on the board
AIR_P-: D24.2 (A), Q13.2 (D); also elsewhere on the board
GND: Q4.3 (S), Q13.3 (S), R17.1, R67.1; also elsewhere on the board
unnamed: Q4.1 (G), R16.1, R17.2
unnamed: Q13.1 (G), R66.1, R67.2
SAFETY_TSMS_IN: D9.1 (K), D24.1 (K); also elsewhere on the board

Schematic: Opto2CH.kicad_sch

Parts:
O4: FOD8802DR2_IMG; SOIC127P600X175-8N; Manufacturer_Part_Number FOD8802DR2; Mouser Part Number 863-FOD8802DR2
R70, R71: 2.7k; R_0603_1608Metric; Manufacturer_Part_Number --
R72, R73: 10k; R_0603_1608Metric; Manufacturer_Part_Number --

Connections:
+3V3: R72.2, R73.2; also elsewhere on the board
/CHARGER_DETECT: O4.8, R72.1; also elsewhere on the board
/SAFETY_DETECT: O4.6, R73.1; also elsewhere on the board
CHARGER_DETECTION: R70.2; also elsewhere on the board
GND: O4.2, O4.4, O4.5, O4.7; also elsewhere on the board
unnamed: O4.1, R70.1
unnamed: O4.3, R71.1
SAFETY_TSMS_IN: R71.2; also elsewhere on the board

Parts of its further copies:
O1, O3: FOD8802DR2_IMG; SOIC127P600X175-8N; Manufacturer_Part_Number FOD8802DR2; Mouser Part Number 863-FOD8802DR2
R20, R21, R62, R63: 2.7k; R_0603_1608Metric; Manufacturer_Part_Number --
R22, R23, R64, R65: 10k; R_0603_1608Metric; Manufacturer_Part_Number --

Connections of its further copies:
+3V3: R22.2, R23.2, R64.2, R65.2; also elsewhere on the board
/AIR_M_DETECT: O3.8, R64.1; also elsewhere on the board
/AIR_PRE_DETECT: O3.6, R65.1; also elsewhere on the board
/AIR_P_DETECT: O1.6, R23.1; also elsewhere on the board
AIR_M_DETECTION: R62.2; also elsewhere on the board
AIR_PRE_DETECTION: R63.2; also elsewhere on the board
AIR_P_DETECTION: R21.2; also elsewhere on the board
EXT_RESET: R20.2; also elsewhere on the board
GND: O1.2, O1.4, O1.5, O1.7, O3.2, O3.4, O3.5, O3.7; also elsewhere on the board
NRST: O1.8, R22.1; also elsewhere on the board
unnamed: O1.1, R20.1
unnamed: O1.3, R21.1
unnamed: O3.1, R62.1
unnamed: O3.3, R63.1

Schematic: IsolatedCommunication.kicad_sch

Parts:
C40: 100nF; C_0603_1608Metric; Manufacturer_Part_Number --
R46, R47: 1k; R_0603_1608Metric; Manufacturer_Part_Number --
U10: LTC6820IMS; MSOP-16_3x4.039mm_P0.5mm; Manufacturer_Part_Number LTC6820IMS#TRPBF; Mouser Part Number 584-LTC6820IMS#TRPBF

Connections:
+3V3: C40.1, U10.1 (EN), U10.6 (Vdds), U10.7 (POL), U10.8 (PHA), U10.9 (Vdd), U10.12 (MSTR); also elsewhere on the board
/Communication/LTC_2_I+: U10.11 (IP); also elsewhere on the board
/Communication/LTC_2_I-: U10.10 (IM); also elsewhere on the board
/LTC_2_~CS: U10.5 (~CS); also elsewhere on the board
/LTC_MISO: U10.3 (MISO); also elsewhere on the board
/LTC_MOSI: U10.2 (MOSI); also elsewhere on the board
/LTC_SCK: U10.4 (SCK); also elsewhere on the board
GND: C40.2, R47.1, U10.13 (SLOW), U10.14 (GND); also elsewhere on the board
unnamed: R46.2, U10.16 (IBIAS)
unnamed: R46.1, R47.2, U10.15 (ICMP)

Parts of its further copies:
C39: 100nF; C_0603_1608Metric; Manufacturer_Part_Number --
R44, R45: 1k; R_0603_1608Metric; Manufacturer_Part_Number --
U9: LTC6820IMS; MSOP-16_3x4.039mm_P0.5mm; Manufacturer_Part_Number LTC6820IMS#TRPBF; Mouser Part Number 584-LTC6820IMS#TRPBF

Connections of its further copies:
+3V3: C39.1, U9.1 (EN), U9.6 (Vdds), U9.7 (POL), U9.8 (PHA), U9.9 (Vdd), U9.12 (MSTR); also elsewhere on the board
/Communication/LTC_1_I+: U9.11 (IP); also elsewhere on the board
/Communication/LTC_1_I-: U9.10 (IM); also elsewhere on the board
/LTC_1_~CS: U9.5 (~CS); also elsewhere on the board
/LTC_MISO: U9.3 (MISO); also elsewhere on the board
/LTC_MOSI: U9.2 (MOSI); also elsewhere on the board
/LTC_SCK: U9.4 (SCK); also elsewhere on the board
GND: C39.2, R45.1, U9.13 (SLOW), U9.14 (GND); also elsewhere on the board
unnamed: R44.2, U9.16 (IBIAS)
unnamed: R44.1, R45.2, U9.15 (ICMP)

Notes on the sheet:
Isolated SPI communication

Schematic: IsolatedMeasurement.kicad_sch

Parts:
C47, C49, C50, C52, C53, C56, C57: 100nF; C_0603_1608Metric; Manufacturer_Part_Number --
C48: 4.7uF; C_0603_1608Metric; Manufacturer_Part_Number --
C51, C54, C55: 10uF; C_0603_1608Metric; Manufacturer_Part_Number --
FB4, FB5: GZ1608D601TF; L_0603_1608Metric; Manufacturer_Part_Number --
IC6: SN74LVC1G07DBVR; SOT-23-5; Mouser Part Number 595-SN74LVC1G07DCKE4
IC7: UCC12040DVE; SOIC-16W_7.5x10.3mm_P1.27mm; Mouser Part Number 595-UCC12040DVE
IC8: ISO6763FDWR; SOIC-16W_7.5x10.3mm_P1.27mm; Mouser Part Number 595-ISO6763FDWR
IC9: AP7365-33YRG-13; AP736533YRG13; Mouser Part Number 621-AP7365-33YRG-13
IC10: REF193GSZ-REEL; SOIC127P600X175-8N; Mouser Part Number 584-REF196GSZ-R
IC11: MCP3561T-E_NC; QFN40P300X300X60-21N-D; Mouser Part Number 579-MCP3561T-E/NC
J8: M300-MV10345M1; M300MV10345M1; Manufacturer_Part_Number M300-MV10345M1; Mouser Part Number 855-M300-MV10345M1
L7: 4.7uH; L_1206_3216Metric; Manufacturer_Part_Number LQM31PN4R7M00L; Mouser Part Number 81-LQM31PN4R7M00L
L8, L9: 1mH; L_1206_3216Metric; Manufacturer_Part_Number LB3218T102K; Mouser Part Number 963-LB3218T102K
R68: 200R; R_0603_1608Metric; Manufacturer_Part_Number --
RD2: CDMM20M0F2500; CDMM; Manufacturer_Part_Number CDMM20M0F2500DET; Mouser Part Number 71-CDMM20M0F2500DET

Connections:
+3V3: C47.1, C49.1, IC6.5, IC8.1 (VCC1); also elsewhere on the board
+5V: L7.1; also elsewhere on the board
/Measurements/Isolated acu measurement/3V_REF: C56.2, IC10.6 (REF_OUT), IC11.2 (REFIN+)
/Measurements/Isolated acu measurement/HV_+3.3V: C50.1, C53.1, C57.1, IC8.16 (VCC2), IC9.3 (VO), IC11.18 (DVDD), L9.1
/Measurements/Isolated acu measurement/HV_+5V: C51.1, C52.2, IC7.13 (SEL), IC7.14 (VISO), IC9.2 (VI), L8.1, R68.2
/Measurements/Isolated acu measurement/HV_SCK: IC8.14 (OUTB), IC11.12 (SCK)
/Measurements/Isolated acu measurement/HV_SDI: IC8.13 (OUTC), IC11.13 (SDI)
/Measurements/Isolated acu measurement/HV_SDO: IC8.12 (IND), IC11.14 (SDO)
/Measurements/Isolated acu measurement/HV_~CS: IC8.15 (OUTA), IC11.11 (~CS)
/~MES_ACU_CS: IC8.2 (INA); also elsewhere on the board
GND: C47.2, C48.2, C49.2, IC6.3, IC7.2 (GNDP), IC7.4 (SYNC), IC7.6 (NC), IC7.7 (NC), IC7.8 (NC), IC8.8 (GND1); also elsewhere on the board
MISO: IC6.4; also elsewhere on the board
MOSI: IC8.4 (INC); also elsewhere on the board
unnamed: FB4.1, L8.2
unnamed: FB5.1, L9.2
unnamed: C48.1, IC7.1 (EN), IC7.3 (VINP), L7.2
unnamed: IC6.2, IC8.5 (OUTD)
unnamed: C54.1, FB4.2, IC10.2 (VSS), IC10.3 (~SLEEP)
unnamed: C55.1, FB5.2, IC11.19 (AVDD)
SCK: IC8.3 (INB); also elsewhere on the board

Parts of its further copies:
C58, C60, C61, C63, C64, C67, C68: 100nF; C_0603_1608Metric; Manufacturer_Part_Number --
C59: 4.7uF; C_0603_1608Metric; Manufacturer_Part_Number --
C62, C65, C66: 10uF; C_0603_1608Metric; Manufacturer_Part_Number --
FB6, FB7: GZ1608D601TF; L_0603_1608Metric; Manufacturer_Part_Number --
IC12: SN74LVC1G07DBVR; SOT-23-5; Mouser Part Number 595-SN74LVC1G07DCKE4
IC13: UCC12040DVE; SOIC-16W_7.5x10.3mm_P1.27mm; Mouser Part Number 595-UCC12040DVE
IC14: ISO6763FDWR; SOIC-16W_7.5x10.3mm_P1.27mm; Mouser Part Number 595-ISO6763FDWR
IC15: AP7365-33YRG-13; AP736533YRG13; Mouser Part Number 621-AP7365-33YRG-13
IC16: REF193GSZ-REEL; SOIC127P600X175-8N; Mouser Part Number 584-REF196GSZ-R
IC17: MCP3561T-E_NC; QFN40P300X300X60-21N-D; Mouser Part Number 579-MCP3561T-E/NC
J9: M300-MV10345M1; M300MV10345M1; Manufacturer_Part_Number M300-MV10345M1; Mouser Part Number 855-M300-MV10345M1
L10: 4.7uH; L_1206_3216Metric; Manufacturer_Part_Number LQM31PN4R7M00L; Mouser Part Number 81-LQM31PN4R7M00L
L11, L12: 1mH; L_1206_3216Metric; Manufacturer_Part_Number LB3218T102K; Mouser Part Number 963-LB3218T102K
R69: 200R; R_0603_1608Metric; Manufacturer_Part_Number --
RD1: CDMM20M0F2500; CDMM; Manufacturer_Part_Number CDMM20M0F2500DET; Mouser Part Number 71-CDMM20M0F2500DET

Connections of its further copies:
+3V3: C58.1, C60.1, IC12.5, IC14.1 (VCC1); also elsewhere on the board
+5V: L10.1; also elsewhere on the board
/Measurements/Isolated car measurement/3V_REF: C67.2, IC16.6 (REF_OUT), IC17.2 (REFIN+)
/Measurements/Isolated car measurement/HV_+3.3V: C61.1, C64.1, C68.1, IC14.16 (VCC2), IC15.3 (VO), IC17.18 (DVDD), L12.1
/Measurements/Isolated car measurement/HV_+5V: C62.1, C63.2, IC13.13 (SEL), IC13.14 (VISO), IC15.2 (VI), L11.1, R69.2
/Measurements/Isolated car measurement/HV_SCK: IC14.14 (OUTB), IC17.12 (SCK)
/Measurements/Isolated car measurement/HV_SDI: IC14.13 (OUTC), IC17.13 (SDI)
/Measurements/Isolated car measurement/HV_SDO: IC14.12 (IND), IC17.14 (SDO)
/Measurements/Isolated car measurement/HV_~CS: IC14.15 (OUTA), IC17.11 (~CS)
/~MES_CAR_CS: IC14.2 (INA); also elsewhere on the board
GND: C58.2, C59.2, C60.2, IC12.3, IC13.2 (GNDP), IC13.4 (SYNC), IC13.6 (NC), IC13.7 (NC), IC13.8 (NC), IC14.8 (GND1); also elsewhere on the board
MISO: IC12.4; also elsewhere on the board
MOSI: IC14.4 (INC); also elsewhere on the board
unnamed: FB6.1, L11.2
unnamed: FB7.1, L12.2
unnamed: C59.1, IC13.1 (EN), IC13.3 (VINP), L10.2
unnamed: IC12.2, IC14.5 (OUTD)
unnamed: C65.1, FB6.2, IC16.2 (VSS), IC16.3 (~SLEEP)
unnamed: C66.1, FB7.2, IC17.19 (AVDD)
SCK: IC14.3 (INB); also elsewhere on the board

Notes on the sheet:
Minimal current - 20mA R - additional load resistor to cap the current draw
SPI iso
3V REF
24bit ADC
ISO
Power

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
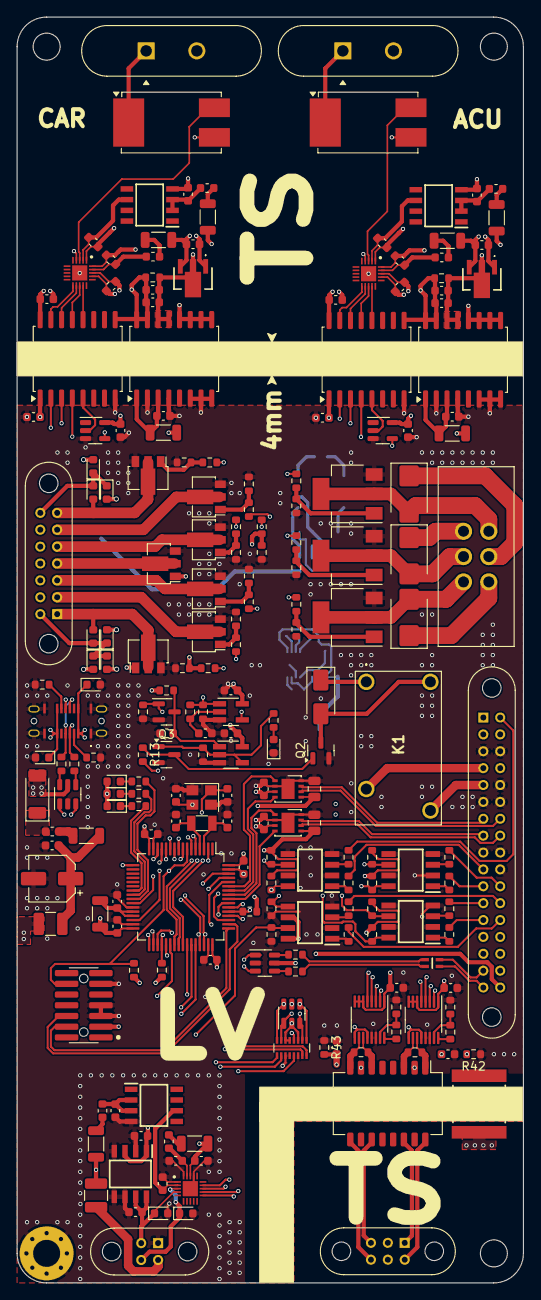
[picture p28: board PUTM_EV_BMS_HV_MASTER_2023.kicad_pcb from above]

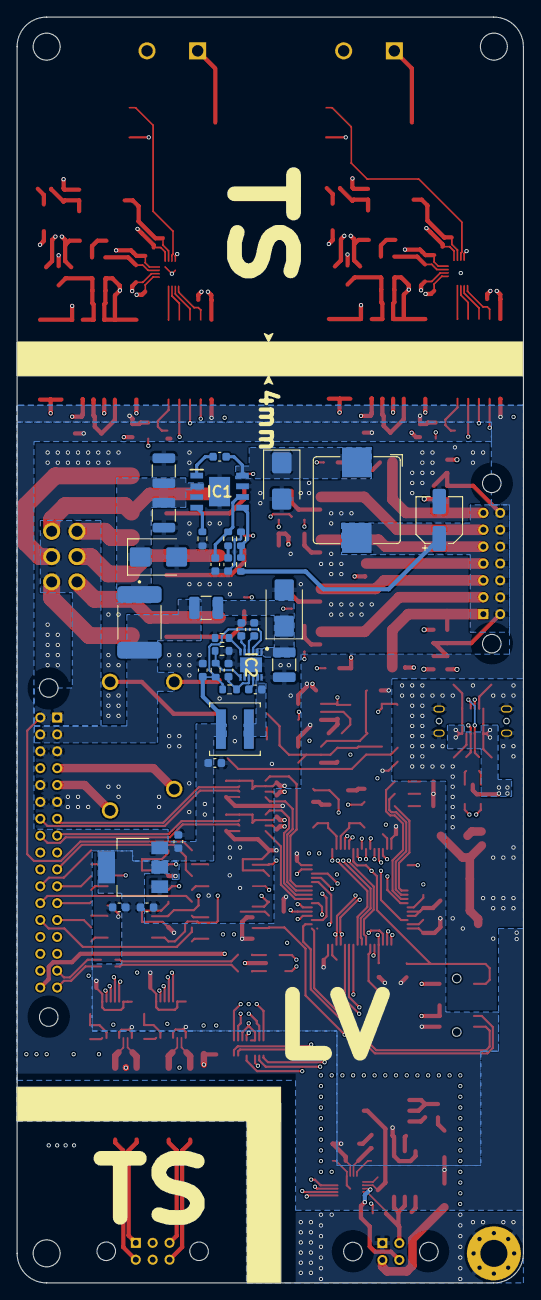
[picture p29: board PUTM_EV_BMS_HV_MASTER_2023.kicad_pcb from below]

Board: 4 copper layers, 60.0 x 150.0 mm, 253 parts (34 on the bottom side), 197 nets.

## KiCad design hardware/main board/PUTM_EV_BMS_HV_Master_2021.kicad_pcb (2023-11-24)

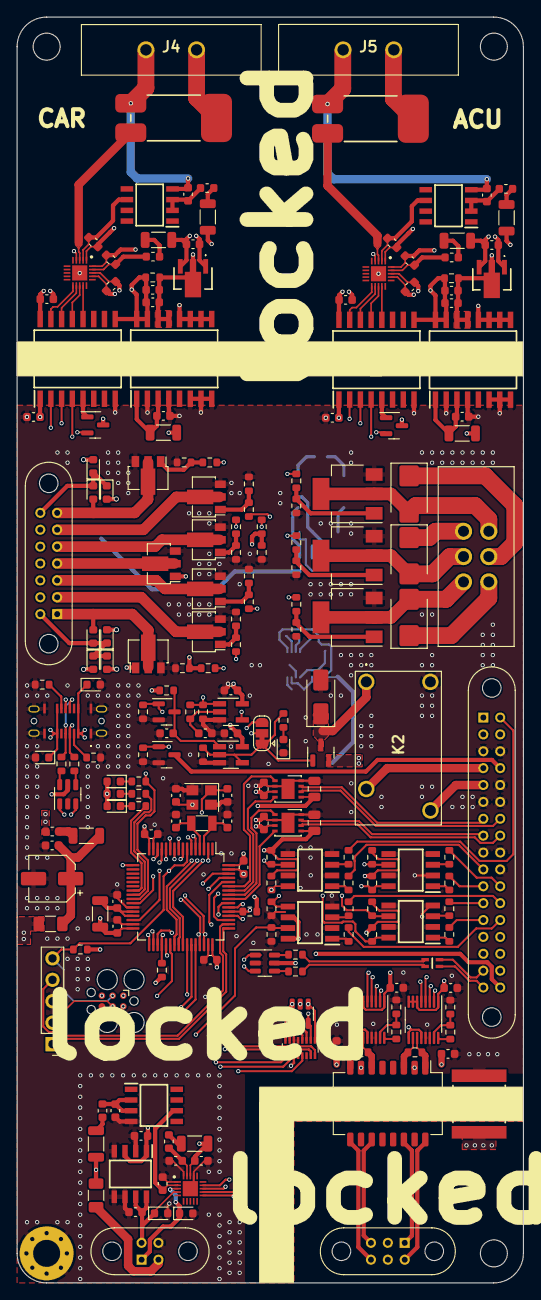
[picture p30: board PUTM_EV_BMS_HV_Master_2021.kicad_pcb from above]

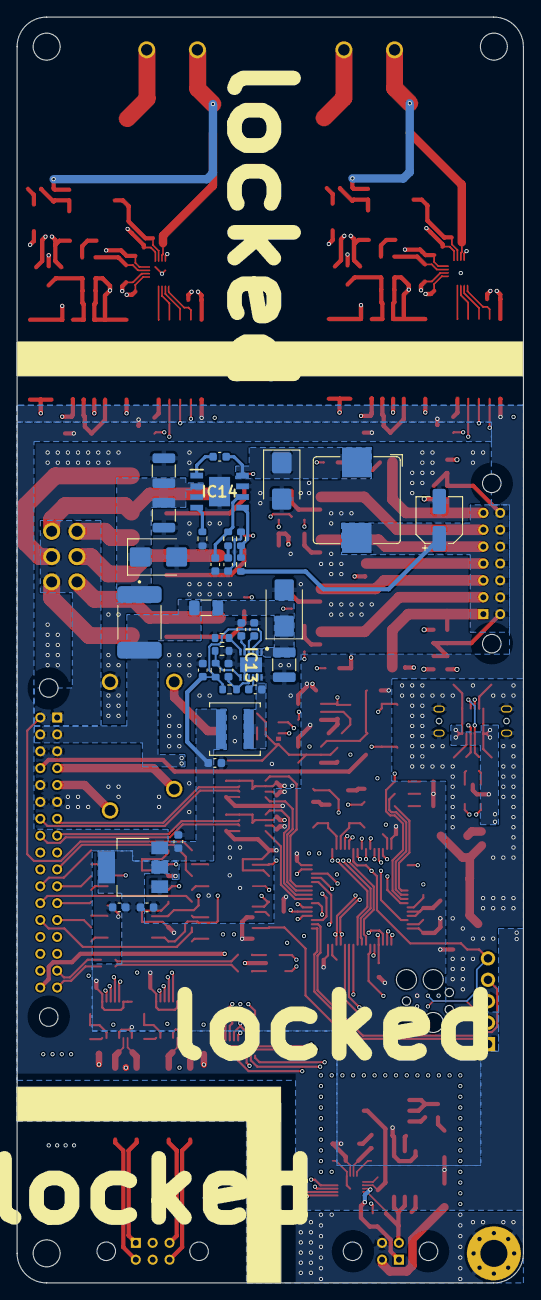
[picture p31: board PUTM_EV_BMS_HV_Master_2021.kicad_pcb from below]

Board: 4 copper layers, 60.0 x 150.0 mm, 250 parts (34 on the bottom side), 197 nets.

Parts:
C1, C7, C9, C22, C26, C37, C46, C55, C56: 10uF; C_0603_1608Metric
C2, C4, C6, C13, C16, C17, C18, C19, C20, C23, C25, C30, C31, C32, C34, C35, C38, C39, C47, C50, C51, C52, C54, C57, C58, C59, C60, C63, C64, C66: 100nF; C_0603_1608Metric
C3, C11: 10uF/60V; C_1210_3225Metric
C5: 1nF; C_0603_1608Metric
C8, C68: 47uF; C_0603_1608Metric
C10, C21: 100nF; C_0805_2012Metric
C12, C15: 1uF; C_0603_1608Metric
C14: 100uF/12V; CP_Elec_5x4.5
C24: 2.2uF/60V; C_1210_3225Metric
C27: 5.6nF; C2824
C28, C29: 22nF; C_0603_1608Metric
C36, C49: 4.7uF; C_0603_1608Metric
C40, C41: 25pF; C_0603_1608Metric
C43, C44: 20pF; C_0603_1608Metric
C61: 12nF; C_0603_1608Metric
C62: 10pF; C_0603_1608Metric
C65, C71: 100nF/60V; C_0603_1608Metric
C67: 2.2uF; C_0603_1608Metric
C69: 5.6nF; C_0603_1608Metric
C72: 47uF/12V; CP_Elec_5x4.5
D1, D21, D22, D23: D_Zener_Small; D_0603_1608Metric
D2: 4A/80V; D_SMB
D3, D11: D_Zener_Small; D_SMB
D4, D12, D13: D_Small; D_SMB
D5, D6, D7, D9: LED_Small_ALT; LED_0603_1608Metric
D8: SP0505BAHT; SOT-23-6
D10: D_Small; D_SMA
D14, D15, D16, D17, D18, D19, D20: D_Schottky_Small; D_0603_1608Metric
F1: 0.5A; Fuse_1206_3216Metric
F2, F3: 1A; Fuse_1206_3216Metric
F4: 24V/5A; 2920L700SLPR
FB1, FB2, FB3, FB4, FB5, FB6, FB7: GZ1608D601TF; L_0603_1608Metric
FL1: DLW21SN501SK2L; DLW21SN121HQ2L
H1, H2, H4: M3; MountingHole_3.2mm_M3
H9: M3; MountingHole_3.2mm_M3_Pad_Via
IC1: MCP1501-10E_SN; SOIC127P600X175-8N
IC2, IC4: MCP3561T-E_NC; QFN40P300X300X60-21N-D
IC3, IC9, IC10: REF193GSZ-REEL; SOIC127P600X175-8N
IC6, IC11: AP7365-33YRG-13; AP736533YRG13
IC7: MCP3562T-E_NC; QFN40P300X300X60-21N-D
IC12, IC17: UCC12040DVE; SOIC127P1030X265-16N
IC13: MAX17643ATC+; SON50P300X300X80-13N
IC14: RTQ2965GSP-QA; SOIC127P600X175-9N
IC15, IC16: ISO6763FDWR; SOIC127P1030X265-16N
J1: USB4145-03-0070-C; USB4145030070C
J2: M80-5103422; M80-51034YY
J4, J5: M300-MV10345M1; M300MV10345M1
J6: M80-5100442; M80-51004YY
J9: M300-MV30645M1; M300MV30645M1
J10: M80-5100622; M80-51006YY
J11: M80-5101422; M80-51014YY
J14: Conn_01x05; PinHeader_1x05_P2.54mm_Vertical
J16: TagConnect; Tag-Connect_TC2030-IDC-FP_2x03_P1.27mm_Vertical
JP4: Cockpit; SolderJumper-3_P1.3mm_Bridged12_RoundedPad1.0x1.5mm
K2: 6-1419128-4; 614191284
L1, L2, L6, L7, L10, L12: LB3218T102K; L_1206_3216Metric
L3: 10uH; L_Bourns_SRP1038C_10.0x10.0mm
L4, L5, L8, L9: 6.8uH; L_1206_3216Metric
L11: 10uH; L_Coilcraft_XAL5050-XXX
O1, O2, O3, O5: FOD8802DR2_IMG; SOIC127P600X175-8N
Q1, Q7, Q9, Q12, Q13, Q14, Q15: 2SK3065; SOT-89-3
Q2, Q4, Q10, Q11: 2N7002; SOT-23
Q3, Q5, Q6: STN4NF06L; SOT-223-3_TabPin2
Q8: AO3400A; SOT-23
R1, R2, R3, R11, R15, R20, R21, R28, R29, R31, R33, R35, R39, R45, R46, R67: 10k; R_0603_1608Metric
R4, R6, R8, R10, R22, R30, R43, R47, R54, R56: 100R; R_0603_1608Metric
R5, R7, R9, R41, R48, R55, R60: 10K; R_0603_1608Metric
R12, R13, R14, R16, R24, R27, R40, R44: 2.7k; R_0603_1608Metric
R17: 4.7R; R_0603_1608Metric
R18, R19: 5.1k; R_0603_1608Metric
R23, R78: 200R; R_0603_1608Metric
R26, R36, R49, R50: 33R; R_0603_1608Metric
R32: 100k; R_0603_1608Metric
R34, R42, R69, R71, R72, R77: 1k; R_0603_1608Metric
R37, R53: 120R; R_0603_1608Metric
R38: 1M; R_0603_1608Metric
R51: 105k; R_0603_1608Metric
R52: 23.2k; R_0603_1608Metric
R57, R58, R62, R63: 1K; R_0603_1608Metric
R59: 40.2k; R_0603_1608Metric
R61: 20.5k; R_0603_1608Metric
R64: 392k; R_0603_1608Metric
R68: 147k; R_0603_1608Metric
R70: 10.5k; R_0603_1608Metric
RD1, RD2: CDMM20M0F2500; CDMM
RN2: 33; R_Array_Convex_8x0602
T1: HM1193NL; Transformer_Pulse_H1100NL
U1, U4: USBLC6-2SC6; SOT-23-6
U2: STM32G484RETx; LQFP-64_10x10mm_P0.5mm
U3, U6: MCP2542FDxMF; DFN-8-1EP_3x3mm_P0.65mm_EP1.55x2.4mm
U5: LM1117-3.3; SOT-223-3_TabPin2
U8: 74LVC1G86; SOT-23-5_HandSoldering
U12, U13: LTC6820IMS; MSOP-16_3x4.039mm_P0.5mm
U14: 74AUP1G32; SOT-23-5_HandSoldering
Y1: X322516MLB4SI; Crystal_SMD_3225-4Pin_3.2x2.5mm
Y2: Q13FC1350000400; Crystal_SMD_3215-2Pin_3.2x1.5mm

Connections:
+3.3VA: C55.1, L4.1, U2.28 (VREF+), U2.29 (VDDA)
+3V3: C2.1, C4.1, C10.2, C15.1, C16.1, C18.1, C21.2, C30.2, C32.1, C34.1, C35.1, C50.1, C51.1, C52.1, C54.1, C57.1, C60.1, C63.2, D5.2 (A), D6.2 (A), D7.2 (A), IC1.1 (VDD), IC1.3 (~SHDN), IC7.18 (DVDD), IC15.1 (VCC1), IC16.1 (VCC1), J14.1, J16.1 (VCC), L4.2, L6.1, O5.6, O5.8, Q10.3 (D), Q11.3 (D), R21.2, R29.2, R31.2, R33.2, R34.2, R35.2, R38.1, R42.2, R45.2, R67.2, U2.16 (VDD), U2.32 (VDD), U2.48 (VDD), U2.64 (VDD), U3.3 (VDD), U3.5 (VIO), U5.2 (VO), U6.3 (VDD), U6.5 (VIO), U8.5 (V), U12.1 (EN), U12.6 (Vdds), U12.7 (POL), U12.8 (PHA), U12.9 (Vdd), U12.12 (MSTR), U13.1 (EN), U13.6 (Vdds), U13.7 (POL), U13.8 (PHA), U13.9 (Vdd), U13.12 (MSTR), U14.5 (V)
+5V: C8.1, C12.1, C68.1, F1.1, F3.1, IC13.3 (~RESET), L1.1, L8.1, L9.1, L11.2, R17.2, R51.2, U5.3 (VI)
+12V: C72.1, D14.1 (K), D15.1 (K), D16.1 (K), D17.1 (K), D18.1 (K), D19.1 (K), D20.1 (K), J11.8, J11.9, J11.10, J11.11, J11.12, J11.13, J11.14, L3.2, R68.2
/AIR_M_DETECT: O3.8, R29.1, U2.26 (PB2)
/AIR_PRE_DETECT: O3.6, R35.1, U2.17 (PA3)
/AIR_P_DETECT: O1.6, R33.1, U2.30 (PB10)
/AMS_FAULT_MCU: R1.2, R32.2, U2.51 (PA15), U8.1
/BOOT: O5.5, R20.2, U2.61 (PB8)
/CHARGER_DETECT: O2.6, R45.1, U2.2 (PC13)
/CLK_IN: C44.1, U2.5 (PF0), Y1.1
/CLK_OUT: C43.2, U2.6 (PF1), Y1.3
/Connectors/LTC_1_OUT_I+: J10.4, T1.16
/Connectors/LTC_1_OUT_I-: J10.1, T1.14
/Connectors/LTC_2_OUT_I+: J10.3, T1.11
/Connectors/LTC_2_OUT_I-: J10.6, T1.9
/Connectors/LTC_CHASSIS: C27.2, J10.2, J10.5
/Connectors/MISO_C: D8.4 (K), J2.33, RN2.9 (R8.2)
/Connectors/MOSI_C: D8.3 (K), J2.32, RN2.10 (R7.2)
/Connectors/SCK_C: D8.5 (K), J2.31, RN2.12 (R5.2)
/Connectors/~EXT_CS_I_C: D8.6 (K), J2.14, RN2.16 (R1.2)
/Connectors/~EXT_CS_V_C: D8.1 (K), J2.15, RN2.15 (R2.2)
/FAN_1_CTRL: R4.2, U2.14 (PA2)
/FAN_2_CTRL: R6.2, U2.13 (PA1)
/FAN_3_CTRL: R8.2, U2.12 (PA0)
/FAN_4_CTRL: R10.2, U2.11 (PC3)
/FAN_5_CTRL: R47.2, U2.10 (PC2)
/FAN_6_CTRL: R54.2, U2.9 (PC1)
/FAN_7_CTRL: R56.2, U2.8 (PC0)
/IMD_SENS_PWM: O5.7, R15.1, U2.38 (PC6)
/LTC_1_~CS: U2.34 (PB12), U12.5 (~CS)
/LTC_2_~CS: U2.33 (PB11), U13.5 (~CS)
/LTC_MISO: R42.1, U2.36 (PB14), U12.3 (MISO), U13.3 (MISO)
/LTC_MOSI: U2.37 (PB15), U12.2 (MOSI), U13.2 (MOSI)
/LTC_SCK: U2.35 (PB13), U12.4 (SCK), U13.4 (SCK)
/MCU_CANFD1_RX: U2.58 (PB5), U6.4 (RXD)
/MCU_CANFD1_TX: U2.59 (PB6), U6.1 (TXD)
/MCU_CANFD2_RX: U2.56 (PB3), U3.4 (RXD)
/MCU_CANFD2_TX: U2.57 (PB4), U3.1 (TXD)
/MCU_D+: U1.3 (I/O2), U2.46 (PA12), U4.3 (I/O2)
/MCU_D-: U1.1 (I/O1), U2.45 (PA11), U4.1 (I/O1)
/MCU_LED_1: R69.1, U2.23 (PC5)
/MCU_LED_2: R71.1, U2.24 (PB0)
/MCU_LED_3: JP4.3 (B), R72.1, U2.25 (PB1)
/Measurements/3V_REF: C6.2, IC3.6 (REF_OUT), IC7.2 (REFIN+)
/Measurements/Isolated acu measurement/3V_REF: C20.2, IC2.2 (REFIN+), IC9.6 (REF_OUT)
/Measurements/Isolated acu measurement/HV_+3.3V: C13.1, C17.1, C39.1, IC2.18 (DVDD), IC6.3 (VO), IC15.16 (VCC2), L10.1
/Measurements/Isolated acu measurement/HV_+5V: C37.1, C38.2, IC6.2 (VI), IC12.13 (SEL), IC12.14 (VISO), L2.1, R23.2
/Measurements/Isolated acu measurement/HV_MES+: IC2.3 (CH0), RD1.3
/Measurements/Isolated acu measurement/HV_SCK: IC2.12 (SCK), IC15.14 (OUTB)
/Measurements/Isolated acu measurement/HV_SDI: IC2.13 (SDI), IC15.13 (OUTC)
/Measurements/Isolated acu measurement/HV_SDO: IC2.14 (SDO), IC15.12 (IND)
/Measurements/Isolated acu measurement/HV_~CS: IC2.11 (~CS), IC15.15 (OUTA)
/Measurements/Isolated car measurement/3V_REF: C47.2, IC4.2 (REFIN+), IC10.6 (REF_OUT)
/Measurements/Isolated car measurement/HV_+3.3V: C23.1, C31.1, C59.1, IC4.18 (DVDD), IC11.3 (VO), IC16.16 (VCC2), L12.1
/Measurements/Isolated car measurement/HV_+5V: C56.1, C58.2, IC11.2 (VI), IC17.13 (SEL), IC17.14 (VISO), L7.1, R78.2
/Measurements/Isolated car measurement/HV_MES+: IC4.3 (CH0), RD2.3
/Measurements/Isolated car measurement/HV_SCK: IC4.12 (SCK), IC16.14 (OUTB)
/Measurements/Isolated car measurement/HV_SDI: IC4.13 (SDI), IC16.13 (OUTC)
/Measurements/Isolated car measurement/HV_SDO: IC4.14 (SDO), IC16.12 (IND)
/Measurements/Isolated car measurement/HV_~CS: IC4.11 (~CS), IC16.15 (OUTA)
/RTC_CLK_IN: C40.2, U2.3 (PC14), Y2.2
/RTC_CLK_OUT: C41.1, U2.4 (PC15), Y2.1
/SAFETY_DETECT: O2.8, R67.1, U2.62 (PB9)
/SIGNAL_AIR_M: R22.2, U2.41 (PC9)
/SIGNAL_AIR_P: R43.2, U2.40 (PC8)
/SIGNAL_AIR_PRE: R30.2, U2.39 (PC7)
/Safeties and related/AMS_FAULT: JP4.1 (A), Q8.1 (G), R11.2, R77.1, U14.2, U14.4
/Safeties and related/CAP_VOLT: C25.2, Q2.3 (D), R38.2, U14.1
/Safeties and related/EDGE_DETECT: Q2.1 (G), R3.1, U8.4
/Safeties and related/IN_DELAY: C64.2, R32.1, U8.2
/~MES_ACU_CS: IC15.2 (INA), U2.60 (PB7)
/~MES_CAR_CS: IC16.2 (INA), U2.55 (PD2)
/~SENS_CS: IC7.11 (~CS), U2.42 (PA8)
AIR_M-: D4.2 (A), J9.3, Q3.2 (D)
AIR_M_DETECTION: J2.13, R24.2
AIR_P-: D13.2 (A), J9.5, Q6.2 (D)
AIR_PRE-: D12.2 (A), J9.4, Q5.2 (D)
AIR_PRE_DETECTION: J2.12, R27.2
AIR_P_DETECTION: J2.28, R16.2
AMS_FAULT_COCKPIT: J2.21, Q4.3 (D)
AMS_SAFETY_1: J2.4, K2.2
AMS_SAFETY_2: J2.5, K2.3
BOOT0: J2.29, R13.2
CANFD1+: J2.7, U6.7 (CANH)
CANFD1-: J2.24, U6.6 (CANL)
CANFD2+: J2.8, U3.7 (CANH)
CANFD2-: J2.25, U3.6 (CANL)
CHARGER_DETECTION: J2.10, R40.2
CUR_SENS_REF: C5.2, D23.1 (K), IC1.7 (OUT), IC1.8 (FB), IC7.4 (CH1), J6.3
CUR_SENS_SIG: D22.1 (K), IC7.3 (CH0), J6.1
D+: J1.A6 (D+), J1.B6 (D+), R49.2
D-: J1.A7 (D-), J1.B7 (D-), R50.1
EXT_RESET: J2.11, R14.2
EX_D+: FL1.4, J2.17
EX_D-: FL1.1, J2.16
EX_VBUS: J2.34, U1.5 (VBUS)
FAN1-: D15.2 (A), J11.1, Q1.2 (D)
FAN2-: D14.2 (A), J11.2, Q7.2 (D)
FAN3-: D16.2 (A), J11.3, Q9.2 (D)
FAN4-: D17.2 (A), J11.4, Q12.2 (D)
FAN5-: D20.2 (A), J11.5, Q13.2 (D)
FAN6-: D19.2 (A), J11.6, Q14.2 (D)
FAN7-: D18.2 (A), J11.7, Q15.2 (D)
GND: C1.2, C2.2, C3.2, C4.2, C5.1, C6.1, C8.2, C10.1, C11.2, C12.2, C14.2, C15.2, C16.2, C18.2, C19.2, C21.1, C24.2, C25.1, C26.2, C27.1, C28.2, C29.2, C30.1, C32.2, C34.2, C35.2, C36.2, C40.1, C41.2, C43.1, C44.2, C49.2, C50.2, C51.2, C52.2, C54.2, C55.2, C57.2, C60.2, C61.2, C62.2, C63.1, C64.1, C66.2, C67.2, C68.2, C69.2, C72.2, D1.2 (A), D2.2 (A), D3.2 (A), D8.2 (A), D9.1 (K), D10.2 (A), D11.2 (A), D21.2 (A), D22.2 (A), D23.2 (A), H9.1, IC1.2 (GND), IC1.4 (GND), IC1.5 (GND), IC1.6 (GND), IC3.4 (GND), IC7.1 (REFIN-), IC7.17 (DGND), IC7.20 (AGND), IC7.21 (EP), IC12.2 (GNDP), IC12.4 (SYNC), IC12.6 (NC), IC12.7 (NC), IC12.8 (NC), IC13.8 (GND), IC13.12 (PGND), IC13.13 (EP), IC14.7 (GND), IC14.9 (EP), IC15.8 (GND1), IC16.8 (GND1), IC17.2 (GNDP), IC17.4 (SYNC), IC17.6 (NC), IC17.7 (NC), IC17.8 (NC), J1.A1 (GND), J1.A12 (GND), J1.B1 (GND), J1.B12 (GND), J1.MH (SHIELD), J2.3, J2.6, J2.9, J2.20, J2.22, J2.23, J2.26, J2.27, J6.4, J14.3, J16.5 (GND), K2.4, O1.2, O1.4, O1.5, O1.7, O2.2, O2.4, O2.5, O2.7, O3.2, O3.4, O3.5, O3.7, O5.2, O5.4, Q1.3 (S), Q2.2 (S), Q3.3 (S), Q4.2 (S), Q5.3 (S), Q6.3 (S), Q7.3 (S), Q9.3 (S), Q12.3 (S), Q13.3 (S), Q14.3 (S), Q15.3 (S), R1.1, R2.2, R3.2, R5.2, R7.2, R9.2, R11.1, R15.2, R18.2, R19.2, R20.1, R28.1, R39.1, R41.2, R46.1, R48.2, R52.1, R55.2, R59.1, R60.2, R62.1, R63.1, R64.1, R70.1, RN2.3 (R3.1), RN2.4 (R4.1), RN2.6 (R6.1), RN2.11 (R6.2), RN2.13 (R4.2), RN2.14 (R3.2), U1.2 (GND), U2.15 (VSS), U2.27 (VSSA), U2.31 (VSS), U2.47 (VSS), U2.63 (VSS), U3.2 (VSS), U3.8 (~STBY), U3.9 (VSS), U4.2 (GND), U5.1 (GND), U6.2 (VSS), U6.8 (~STBY), U6.9 (VSS), U8.3 (G), U12.13 (SLOW), U12.14 (GND), U13.13 (SLOW), U13.14 (GND), U14.3 (G), Y1.2, Y1.4
HV_ACU+: J5.3, RD1.1
HV_ACU-: C7.2, C9.2, C13.2, C17.2, C20.1, C37.2, C38.1, C39.2, IC2.1 (REFIN-), IC2.4 (CH1), IC2.17 (DGND), IC2.20 (AGND), IC2.21 (EP), IC6.1 (GND), IC9.4 (GND), IC12.9 (GNDS), IC12.10 (NCS), IC12.11 (NCS), IC12.12 (NCS), IC12.15 (GNDS), IC12.16 (GNDS), IC15.9 (GND2), J5.1, R23.1, RD1.2
HV_CAR+: J4.3, RD2.1
HV_CAR-: C22.2, C23.2, C31.2, C46.2, C47.1, C56.2, C58.1, C59.2, IC4.1 (REFIN-), IC4.4 (CH1), IC4.17 (DGND), IC4.20 (AGND), IC4.21 (EP), IC10.4 (GND), IC11.1 (GND), IC16.9 (GND2), IC17.9 (GNDS), IC17.10 (NCS), IC17.11 (NCS), IC17.12 (NCS), IC17.15 (GNDS), IC17.16 (GNDS), J4.1, R78.1, RD2.2
IMD_SENSENSOR: J2.30, R12.2
LTC_1_I+: R53.2, T1.1, U12.11 (IP)
LTC_1_I-: R53.1, T1.3, U12.10 (IM)
LTC_2_I+: R37.2, T1.6, U13.11 (IP)
LTC_2_I-: R37.1, T1.8, U13.10 (IM)
MISO: IC7.14 (SDO), Q10.2 (S), Q11.2 (S), R34.1, RN2.8 (R8.1), U2.53 (PC11)
MOSI: IC7.13 (SDI), IC15.4 (INC), IC16.4 (INC), RN2.7 (R7.1), U2.54 (PC12)
NRST: J14.5, J16.3 (~RESET), O1.8, R21.1, R31.1, U2.7 (PG10)
unnamed: C14.1, C19.1, F3.2, L5.2
unnamed: C28.1, T1.2
unnamed: C29.1, T1.7
unnamed: C61.1, R61.1
unnamed: C71.2, D2.1 (K), IC14.8 (SW), L3.1
unnamed: C3.1, C11.1, D3.1 (K), F4.1, IC14.2 (VIN)
unnamed: D5.1 (K), R69.2
unnamed: D6.1 (K), R71.2
unnamed: D7.1 (K), R72.2
unnamed: D9.2 (A), R77.2
unnamed: D10.1 (K), K2.1, Q8.3 (D)
unnamed: C24.1, D11.1 (K), F2.1, IC13.1 (VIN), IC13.2 (EN/UVLO)
unnamed: F1.2, J6.2
unnamed: FB1.1, L5.1
unnamed: FB2.1, L2.2
unnamed: FB3.1, L7.2
unnamed: FB4.1, L10.2
unnamed: FB5.1, L12.2
unnamed: FB6.1, L6.2
unnamed: FB7.1, L1.2
unnamed: FL1.2, R36.1
unnamed: FL1.3, R26.2
unnamed: C7.1, FB4.2, IC2.19 (AVDD)
unnamed: C1.1, FB7.2, IC3.2 (VSS), IC3.3 (~SLEEP)
unnamed: C22.1, FB5.2, IC4.19 (AVDD)
unnamed: C26.1, FB6.2, IC7.19 (AVDD)
unnamed: C9.1, FB2.2, IC9.2 (VSS), IC9.3 (~SLEEP)
unnamed: C46.1, FB3.2, IC10.2 (VSS), IC10.3 (~SLEEP)
unnamed: C36.1, IC12.1 (EN), IC12.3 (VINP), L8.2
unnamed: C65.1, IC13.10 (BST)
unnamed: C66.1, IC13.9 (EXTVCC), R17.1
unnamed: IC13.7 (FB), R51.1, R52.2
unnamed: C65.2, IC13.11 (LX), L11.1
unnamed: IC13.6 (RT/SYNC), R59.2
unnamed: C69.1, IC13.4 (SS)
unnamed: C67.1, IC13.5 (VCC)
unnamed: C71.1, IC14.1 (BOOT)
unnamed: C62.1, IC14.6 (COMP), R61.2
unnamed: IC14.5 (FB), R68.1, R70.2
unnamed: IC14.4 (RT/SYNC), R64.2
unnamed: IC15.5 (OUTD), Q10.1 (G)
unnamed: IC16.5 (OUTD), Q11.1 (G)
unnamed: C49.1, IC17.1 (EN), IC17.3 (VINP), L9.2
unnamed: J1.A5 (CC1), R18.1
unnamed: J1.B5 (CC2), R19.1
unnamed: JP4.2 (C), Q4.1 (G), R2.1
unnamed: O1.1, R14.1
unnamed: O1.3, R16.1
unnamed: O2.1, R40.1
unnamed: O2.3, R44.1
unnamed: O3.1, R24.1
unnamed: O3.3, R27.1
unnamed: O5.1, R12.1
unnamed: O5.3, R13.1
unnamed: Q1.1 (G), R4.1, R5.1
unnamed: Q3.1 (G), R22.1, R28.2
unnamed: Q5.1 (G), R30.1, R39.2
unnamed: Q6.1 (G), R43.1, R46.2
unnamed: Q7.1 (G), R6.1, R7.1
unnamed: Q9.1 (G), R8.1, R9.1
unnamed: Q12.1 (G), R10.1, R41.1
unnamed: Q13.1 (G), R47.1, R48.1
unnamed: Q14.1 (G), R54.1, R55.1
unnamed: Q15.1 (G), R56.1, R60.1
unnamed: R26.1, U1.4 (I/O2)
unnamed: R36.2, U1.6 (I/O1)
unnamed: R49.1, U4.4 (I/O2)
unnamed: R50.2, U4.6 (I/O1)
unnamed: R57.2, U12.16 (IBIAS)
unnamed: R57.1, R62.2, U12.15 (ICMP)
unnamed: R58.2, U13.16 (IBIAS)
unnamed: R58.1, R63.2, U13.15 (ICMP)
SAFETY_TSMS_IN: D4.1 (K), D12.1 (K), D13.1 (K), J2.1, J2.18, J9.1, J9.2, J9.6, R44.2
SCK: IC7.12 (SCK), IC15.3 (INB), IC16.3 (INB), RN2.5 (R5.1), U2.52 (PC10)
SWCLK: J14.2, J16.4 (SWCLK), U2.50 (PA14)
SWDIO: J14.4, J16.2 (SWDIO), U2.49 (PA13)
VBUS: D1.1 (K), D21.1 (K), FB1.2, J1.A4 (VBUS), J1.A9 (VBUS), J1.B4 (VBUS), J1.B9 (VBUS), U4.5 (VBUS)
VDD: F2.2, F4.2, J2.2, J2.19, Q8.2 (S)
~EXT_CS_I: RN2.1 (R1.1), U2.44 (PA10)
~EXT_CS_V: RN2.2 (R2.1), U2.43 (PA9)

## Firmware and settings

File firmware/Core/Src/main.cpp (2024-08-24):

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
/* Includes ------------------------------------------------------------------*/
#include "main.h"
#include "cmsis_os.h"
#include "adc.h"
#include "dma.h"
#include "fdcan.h"
#include "rtc.h"
#include "spi.h"
#include "tim.h"
#include "usb_device.h"
#include "gpio.h"

/* USER CODE BEGIN Includes */
#include <FreeRTOS.h>
#include <app_freertos.h>
#include <Controllers/GpioController.hpp>
#include <Controllers/Ltc6811Controller.hpp>
#include <Controllers/Mcp356xController.hpp>
#include <Controllers/SpiDmaController.hpp>
#include <StackData.hpp>
/* USER CODE END Includes */


/* USER CODE BEGIN PV */
GpioOut led_ok 			{ LED1_GPIO_Port, LED1_Pin, true };
GpioOut led_warning 	{ LED2_GPIO_Port, LED2_Pin, true };
GpioOut led_error 		{ LED3_GPIO_Port, LED3_Pin, true };
GpioOut ams_status 		{ AMS_FAULT_GPIO_Port, AMS_FAULT_Pin, false };
GpioIn  charger_detect 	{ CHARGER_DETECT_GPIO_Port, CHARGER_DETECT_Pin, true };
GpioIn 	safety_detect	{ SAFETY_DETECT_GPIO_Port, SAFETY_DETECT_Pin, true };
GpioIn 	air_m_detect	{ AIR_M_DETECT_GPIO_Port, AIR_M_DETECT_Pin };
GpioIn 	air_p_detect	{ AIR_P_DETECT_GPIO_Port, AIR_P_DETECT_Pin };
GpioIn 	air_pre_detect	{ AIR_PRE_DETECT_GPIO_Port, AIR_PRE_DETECT_Pin };
/* USER CODE END PV */

void SystemClock_Config(void);
void MX_FREERTOS_Init(void);
/**
  * @brief  The application entry point.
  * @retval int
  */
int main(void)
{

  /* MCU Configuration--------------------------------------------------------*/

  /* Reset of all peripherals, Initializes the Flash interface and the Systick. */
  HAL_Init();

  /* Configure the system clock */
  SystemClock_Config();

  /* Initialize all configured peripherals */
  MX_GPIO_Init();
  MX_DMA_Init();
  MX_FDCAN2_Init();
  MX_FDCAN3_Init();
  MX_RTC_Init();
  MX_SPI1_Init();
  MX_SPI2_Init();
  MX_SPI3_Init();
  MX_TIM1_Init();
  MX_TIM2_Init();
  MX_TIM3_Init();
  MX_ADC1_Init();
  MX_ADC3_Init();
  /* USER CODE BEGIN 2 */
  //SpiDmaController::initSpiDmaManager();
  led_ok.deactivate();
  led_warning.deactivate();
  led_error.deactivate();

  ams_status.toggle();
  //HAL_Delay(10);
  //ams_status.toggle();
  /* USER CODE END 2 */

  /* Init scheduler */
  osKernelInitialize();

  /* Call init function for freertos objects (in cmsis_os2.c) */
  MX_FREERTOS_Init();

  /* Start scheduler */
  osKernelStart();

  /* We should never get here as control is now taken by the scheduler */

  /* Infinite loop */
  /* USER CODE BEGIN WHILE */
  while (1)
  {
    /* USER CODE END WHILE */

    /* USER CODE BEGIN 3 */
  }
  /* USER CODE END 3 */
}

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
/**
  * @brief  Period elapsed callback in non blocking mode
  * @note   This function is called  when TIM4 interrupt took place, inside
  * HAL_TIM_IRQHandler(). It makes a direct call to HAL_IncTick() to increment
  * a global variable "uwTick" used as application time base.
  * @param  htim : TIM handle
  * @retval None
  */
void HAL_TIM_PeriodElapsedCallback(TIM_HandleTypeDef *htim)
{
  if (htim->Instance == TIM4) {
    HAL_IncTick();
  }
}

/**
  * @brief  This function is executed in case of error occurrence.
  * @retval None
  */
void Error_Handler(void)
{
  /* USER CODE BEGIN Error_Handler_Debug */
  /* User can add his own implementation to report the HAL error return state */
  //__disable_irq();
  vTaskSuspendAll();
  while (1)
  {
  }
  /* USER CODE END Error_Handler_Debug */
}

#ifdef  USE_FULL_ASSERT
/**
  * @brief  Reports the name of the source file and the source line number
  *         where the assert_param error has occurred.
  * @param  file: pointer to the source file name
  * @param  line: assert_param error line source number
  * @retval None
  */
void assert_failed(uint8_t *file, uint32_t line)
{
  /* USER CODE BEGIN 6 */
  /* User can add his own implementation to report the file name and line number,
     ex: printf("Wrong parameters value: file %s on line %d\r\n", file, line) */
  /* USER CODE END 6 */
}
#endif /* USE_FULL_ASSERT */

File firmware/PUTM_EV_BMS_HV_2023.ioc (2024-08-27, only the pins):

Mcu.UserName=STM32G484RETx
PA0.GPIO_Label=FAN_CTRL3
PA0.Signal=S_TIM2_CH1
PA1.GPIO_Label=FAN_CTRL2
PA1.Signal=S_TIM2_CH2
PA10.GPIO_Label=NMES_EXT_I_CS
PA10.Signal=GPIO_Output
PA11.Signal=USB_DM
PA12.Signal=USB_DP
PA13.Signal=SYS_JTMS-SWDIO
PA14.Signal=SYS_JTCK-SWCLK
PA15.GPIO_Label=AMS_FAULT
PA15.Signal=GPIO_Output
PA2.GPIO_Label=FAN_CTRL1
PA2.Signal=GPIO_Output
PA3.GPIO_Label=AIR_PRE_DETECT
PA3.Signal=GPIO_Input
PA4.GPIO_Label=CARD_DETECT
PA4.Signal=GPIO_Input
PA5.GPIO_Label=CARD_SCK
PA5.Signal=SPI1_SCK
PA6.GPIO_Label=CARD_MISO
PA6.Signal=SPI1_MISO
PA7.GPIO_Label=CARD_MOSI
PA7.Signal=SPI1_MOSI
PA8.GPIO_Label=NMES_ISENS_CS
PA8.Signal=GPIO_Output
PA9.GPIO_Label=NMES_EXT_V_CS
PA9.Signal=GPIO_Output
PB0.GPIO_Label=LED2
PB0.Signal=GPIO_Output
PB1.GPIO_Label=LED3
PB1.Signal=GPIO_Output
PB10.GPIO_Label=AIR_P_DETECT
PB10.Signal=GPIO_Input
PB11.GPIO_Label=NLTC2_CS
PB11.Signal=GPIO_Output
PB12.GPIO_Label=NLTC1_CS
PB12.Signal=GPIO_Output
PB13.GPIO_Label=LTC_SCK
PB13.Signal=SPI2_SCK
PB14.GPIO_Label=LTC_MISO
PB14.Signal=SPI2_MISO
PB15.GPIO_Label=LTC_MOSI
PB15.Signal=SPI2_MOSI
PB2.GPIO_Label=AIR_M_DETECT
PB2.Signal=GPIO_Input
PB3.GPIO_Label=FDCAN1_RX
PB3.Signal=FDCAN3_RX
PB4.GPIO_Label=FDCAN1_TX
PB4.Signal=FDCAN3_TX
PB5.Signal=FDCAN2_RX
PB6.Signal=FDCAN2_TX
PB7.GPIO_Label=NMES_ACU_CS
PB7.Signal=GPIO_Output
PB9.GPIO_Label=CHARGER_DETECT
PB9.Signal=GPIO_Input
PC0.GPIO_Label=FAN_CTRL7
PC0.Signal=S_TIM1_CH1
PC1.GPIO_Label=FAN_CTRL6
PC1.Signal=S_TIM1_CH2
PC10.GPIO_Label=MES_SCK
PC10.Signal=SPI3_SCK
PC11.GPIO_Label=MES_MISO
PC11.Signal=SPI3_MISO
PC12.GPIO_Label=MES_MOSI
PC12.Signal=SPI3_MOSI
PC13.GPIO_Label=SAFETY_DETECT
PC13.Signal=GPIO_Input
PC14-OSC32_IN.Signal=RCC_OSC32_IN
PC15-OSC32_OUT.Signal=RCC_OSC32_OUT
PC2.GPIO_Label=FAN_CTRL5
PC2.Signal=S_TIM1_CH3
PC3.GPIO_Label=FAN_CTRL4
PC3.Signal=S_TIM1_CH4
PC4.GPIO_Label=NCARD_CS
PC4.Signal=GPIO_Output
PC5.GPIO_Label=LED1
PC5.Signal=GPIO_Output
PC6.Signal=S_TIM3_CH1
PC7.GPIO_Label=SIG_AIR_PRE
PC7.Signal=GPIO_Output
PC8.GPIO_Label=SIG_AIR_P
PC8.Signal=GPIO_Output
PC9.GPIO_Label=SIG_AIR_M
PC9.Signal=GPIO_Output
PD2.GPIO_Label=NMES_CAR_CS
PD2.Signal=GPIO_Output
PF0-OSC_IN.Signal=RCC_OSC_IN
PF1-OSC_OUT.Signal=RCC_OSC_OUT

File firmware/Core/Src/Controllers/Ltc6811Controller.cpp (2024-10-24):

/*
 * LTCController.cpp
 *
 *  Created on: 19 lip 2023
 *      Author: piotr
 */

#include <Controllers/Ltc6811Controller.hpp>
#include <Controllers/SpiDmaController.hpp>
#include <Utils/PEC15.hpp>
#include <algorithm>
#include <bitset>

using namespace Ltc6811;
using namespace LtcConfig;

Ltc6811Controller::Ltc6811Controller(GpioOut cs, SPI_HandleTypeDef &hspi) : hspi(hspi), cs(cs)
{
	//cs.deactivate();

	//for(auto cfg : configs)
	for(size_t i = 0; i < CHAIN_SIZE; i++)
	{
		// set gpio pull down to OFF
		configs[i].gpio1 = 1;
		configs[i].gpio2 = 1;
		configs[i].gpio3 = 1;
		configs[i].gpio4 = 1;
		configs[i].gpio5 = 1;
		// set reference to shut down after conversion
		configs[i].refon = 0;
		// set adc clock to use higher speeds
		configs[i].adcopt = 1;
		// set all discharges to off
		configs[i].dcc1 = 0;
		configs[i].dcc2 = 0;
		configs[i].dcc3 = 0;
		configs[i].dcc4 = 0;
		configs[i].dcc5 = 0;
		configs[i].dcc6 = 0;
		configs[i].dcc7 = 0;
		configs[i].dcc8 = 0;
		configs[i].dcc9 = 0;
		configs[i].dcc10 = 0;
		configs[i].dcc11 = 0;
		configs[i].dcc12 = 0;
		//set under voltage comparison voltage
		configs[i].vuv = vuv;
		//set over voltage comparison voltage
		configs[i].vov = vov;
		//set soft watch dog timer discharge time (can't be used in our case)
		configs[i].dcto = DischargeTime::Disable;
	}
}

template < Ltc6811::ReadRegisterGroup RdReg >
LtcStatus Ltc6811Controller::rawRead(Ltc6811::RCmd cmd, RegArray < RdReg > *out, RegArray < LtcStatus > *out_pec)
{
	auto status = LtcStatus::Ok;

	static std::array < uint8_t, 4 + CHAIN_SIZE * 8 > stxdata { 0 };
	static std::array < uint8_t, 4 + CHAIN_SIZE * 8 > srxdata { 0 };

	auto stxdit = stxdata.begin();
	auto srxdit = srxdata.begin() + 4;
	auto odit	= out->begin();
	auto opit	= out_pec->begin();

	std::tie(stxdit[0], stxdit[1]) = serializeCmd(cmd);
	std::tie(stxdit[2], stxdit[3]) = calcPEC(stxdit, stxdit + 2);

	SpiTxRxRequest request(cs, hspi, stxdata.begin(), srxdata.begin(), stxdata.size());
	SpiDmaController::spiRequestAndWait(request);

	for(size_t i = 0; i < LtcConfig::CHAIN_SIZE; i++)
	{
		auto srxditbeg 	= srxdit;
		auto srxditend 	= srxdit + 6;
		auto srxp0		= *(srxdit + 6);
		auto srxp1		= *(srxdit + 7);

		auto [ pec0, pec1 ] = calcPEC(srxditbeg, srxditend);
		if( pec0 != srxp0 || pec1 != srxp1)
		{
			*opit = LtcStatus::PecError;
			status = LtcStatus::PecError;
		}
		else
		{
			*opit = LtcStatus::Ok;
			deserializeRegisterGroup(odit, srxdit);
		}

		srxdit 	+= 8;
		odit	+= 1;
		opit	+= 1;
	}

	return status;
}

template < WriteReadRegisterGroup WrRdReg >
LtcStatus Ltc6811Controller::rawWrite(Ltc6811::WCmd cmd, RegArray < WrRdReg > const *data)
{
	auto status = LtcStatus::Ok;

	static std::array < uint8_t, 4 + CHAIN_SIZE * 8 > stxdata;
	auto stxdit = stxdata.begin();

	std::tie(stxdit[0], stxdit[1]) = serializeCmd(cmd);
	std::tie(stxdit[2], stxdit[3]) = calcPEC(stxdit, stxdit + 2);
	stxdit += 4;

	for(auto rdit = data->rbegin(); rdit != data->rend(); rdit++)
	{
		serializeRegisterGroup(stxdit, *rdit);
		std::tie(stxdit[6], stxdit[7]) = calcPEC(stxdit, stxdit + 6);
		stxdit += 8;
	}

	SpiTxRequest request(cs, hspi, stxdata.begin(), stxdata.size());
	SpiDmaController::spiRequestAndWait(request);

	return status;
}
LtcStatus Ltc6811Controller::rawWrite(Ltc6811::WCmd cmd)
{
	auto status = LtcStatus::Ok;

	static std::array < uint8_t, 4 > stxdata;
	auto stxdit = stxdata.begin();

	std::tie(stxdit[0], stxdit[1]) = serializeCmd(cmd);
	std::tie(stxdit[2], stxdit[3]) = calcPEC(stxdit, stxdit + 2);

	SpiTxRequest request(cs, hspi, stxdata.begin(), stxdata.size());
	SpiDmaController::spiRequestAndWait(request);

	return status;
}

void Ltc6811Controller::wakeUp()
{
	uint8_t dummy = 0;
	SpiTxRequest request(cs, hspi, &dummy, 1);
	SpiDmaController::spiRequestAndWait(request);
	osDelay(twake_full);
}

void Ltc6811Controller::handleWatchDog()
{
	rawWrite(CMD_PLADC);
}

LtcStatus Ltc6811Controller::configure()
{
	wakeUp();
	return rawWrite(CMD_WRCFGA, &configs);
}

LtcStatus Ltc6811Controller::readPdVoltages(DataArray < float > *out)
{
	auto status = LtcStatus::Ok;

	static std::array < RegArray < CellVoltage >, 4> regs;
	static std::array < RegArray < LtcStatus >, 4 > pecs;

	for(size_t repeat = 0; repeat < 2; repeat++)
	{
		wakeUp();
		//rawWrite(CMD_ADOW(Mode::Normal, Pull::Down, Discharge::NotPermited, Cell::All));
		rawWrite(CMD_ADCV(Mode::Normal, Discharge::NotPermited, Cell::All));
		osDelay(tadc);
	}

	wakeUp();
	rawRead(CMD_RDCVA, &regs[0], &pecs[0]);
	//wakeUp();
	rawRead(CMD_RDCVB, &regs[1], &pecs[1]);
	//wakeUp();
	rawRead(CMD_RDCVC, &regs[2], &pecs[2]);
	//wakeUp();
	rawRead(CMD_RDCVD, &regs[3], &pecs[3]);

	for(size_t ltc = 0; ltc < CHAIN_SIZE; ltc++)
	{
		for(size_t r = 0; r < 3; r++)
		{
			if(pecs[r][ltc] == LtcStatus::Ok)
			{
				out->at(ltc*12 + r*3 + 0) = convRawToU(regs[r][ltc].channel[0].val);
				out->at(ltc*12 + r*3 + 1) = convRawToU(regs[r][ltc].channel[1].val);
				out->at(ltc*12 + r*3 + 2) = convRawToU(regs[r][ltc].channel[2].val);
			}
			else
			{
				out->at(ltc*12 + r*3 + 0) = -1.0f;
				out->at(ltc*12 + r*3 + 1) = -1.0f;
				out->at(ltc*12 + r*3 + 2) = -1.0f;
			}
		}
	}

	return status;
}
LtcStatus Ltc6811Controller::readPuVoltages(DataArray < float > *out)
{
	auto status = LtcStatus::Ok;

	static std::array < RegArray < CellVoltage >, 4> regs;
	static std::array < RegArray < LtcStatus >, 4 > pecs;

	for(size_t repeat = 0; repeat < 2; repeat++)
	{
		wakeUp();
		rawWrite(CMD_ADOW(Mode::Filtered, Pull::Up, Discharge::NotPermited, Cell::All));
		//rawWrite(CMD_ADCV(Mode::Normal, Discharge::NotPermited, Cell::All));
		osDelay(tadc);
	}

	wakeUp();
	rawRead(CMD_RDCVA, &regs[0], &pecs[0]);
	//wakeUp();
	rawRead(CMD_RDCVB, &regs[1], &pecs[1]);
	//wakeUp();
	rawRead(CMD_RDCVC, &regs[2], &pecs[2]);
	//wakeUp();
	rawRead(CMD_RDCVD, &regs[3], &pecs[3]);

	for(size_t ltc = 0; ltc < CHAIN_SIZE; ltc++)
	{
		for(size_t r = 0; r < 4; r++)
		{
			if(pecs[r][ltc] == LtcStatus::Ok)
			{
				out->at(ltc*12 + r*3 + 0) = convRawToU(regs[r][ltc].channel[0].val);
				out->at(ltc*12 + r*3 + 1) = convRawToU(regs[r][ltc].channel[1].val);
				out->at(ltc*12 + r*3 + 2) = convRawToU(regs[r][ltc].channel[2].val);
			}
			else
			{
				out->at(ltc*12 + r*3 + 0) = -1.0f;
				out->at(ltc*12 + r*3 + 1) = -1.0f;
				out->at(ltc*12 + r*3 + 2) = -1.0f;
			}
		}
	}

	return status;
}
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

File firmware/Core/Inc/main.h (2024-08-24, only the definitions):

#define SAFETY_DETECT_Pin GPIO_PIN_13
#define SAFETY_DETECT_GPIO_Port GPIOC
#define FAN_CTRL7_Pin GPIO_PIN_0
#define FAN_CTRL7_GPIO_Port GPIOC
#define FAN_CTRL6_Pin GPIO_PIN_1
#define FAN_CTRL6_GPIO_Port GPIOC
#define FAN_CTRL5_Pin GPIO_PIN_2
#define FAN_CTRL5_GPIO_Port GPIOC
#define FAN_CTRL4_Pin GPIO_PIN_3
#define FAN_CTRL4_GPIO_Port GPIOC
#define FAN_CTRL3_Pin GPIO_PIN_0
#define FAN_CTRL3_GPIO_Port GPIOA
#define FAN_CTRL2_Pin GPIO_PIN_1
#define FAN_CTRL2_GPIO_Port GPIOA
#define FAN_CTRL1_Pin GPIO_PIN_2
#define FAN_CTRL1_GPIO_Port GPIOA
#define AIR_PRE_DETECT_Pin GPIO_PIN_3
#define AIR_PRE_DETECT_GPIO_Port GPIOA
#define CARD_DETECT_Pin GPIO_PIN_4
#define CARD_DETECT_GPIO_Port GPIOA
#define CARD_SCK_Pin GPIO_PIN_5
#define CARD_SCK_GPIO_Port GPIOA
#define CARD_MISO_Pin GPIO_PIN_6
#define CARD_MISO_GPIO_Port GPIOA
#define CARD_MOSI_Pin GPIO_PIN_7
#define CARD_MOSI_GPIO_Port GPIOA
#define NCARD_CS_Pin GPIO_PIN_4
#define NCARD_CS_GPIO_Port GPIOC
#define LED1_Pin GPIO_PIN_5
#define LED1_GPIO_Port GPIOC
#define LED2_Pin GPIO_PIN_0
#define LED2_GPIO_Port GPIOB
#define LED3_Pin GPIO_PIN_1
#define LED3_GPIO_Port GPIOB
#define AIR_M_DETECT_Pin GPIO_PIN_2
#define AIR_M_DETECT_GPIO_Port GPIOB
#define AIR_P_DETECT_Pin GPIO_PIN_10
#define AIR_P_DETECT_GPIO_Port GPIOB
#define NLTC2_CS_Pin GPIO_PIN_11
#define NLTC2_CS_GPIO_Port GPIOB
#define NLTC1_CS_Pin GPIO_PIN_12
#define NLTC1_CS_GPIO_Port GPIOB
#define LTC_SCK_Pin GPIO_PIN_13
#define LTC_SCK_GPIO_Port GPIOB
#define LTC_MISO_Pin GPIO_PIN_14
#define LTC_MISO_GPIO_Port GPIOB
#define LTC_MOSI_Pin GPIO_PIN_15
#define LTC_MOSI_GPIO_Port GPIOB
#define SIG_AIR_PRE_Pin GPIO_PIN_7
#define SIG_AIR_PRE_GPIO_Port GPIOC
#define SIG_AIR_P_Pin GPIO_PIN_8
#define SIG_AIR_P_GPIO_Port GPIOC
#define SIG_AIR_M_Pin GPIO_PIN_9
#define SIG_AIR_M_GPIO_Port GPIOC
#define NMES_ISENS_CS_Pin GPIO_PIN_8
#define NMES_ISENS_CS_GPIO_Port GPIOA
#define NMES_EXT_V_CS_Pin GPIO_PIN_9
#define NMES_EXT_V_CS_GPIO_Port GPIOA
#define NMES_EXT_I_CS_Pin GPIO_PIN_10
#define NMES_EXT_I_CS_GPIO_Port GPIOA
#define AMS_FAULT_Pin GPIO_PIN_15
#define AMS_FAULT_GPIO_Port GPIOA
#define MES_SCK_Pin GPIO_PIN_10
#define MES_SCK_GPIO_Port GPIOC
#define MES_MISO_Pin GPIO_PIN_11
#define MES_MISO_GPIO_Port GPIOC
#define MES_MOSI_Pin GPIO_PIN_12
#define MES_MOSI_GPIO_Port GPIOC
#define NMES_CAR_CS_Pin GPIO_PIN_2
#define NMES_CAR_CS_GPIO_Port GPIOD
#define FDCAN1_RX_Pin GPIO_PIN_3
#define FDCAN1_RX_GPIO_Port GPIOB
#define FDCAN1_TX_Pin GPIO_PIN_4
#define FDCAN1_TX_GPIO_Port GPIOB
#define NMES_ACU_CS_Pin GPIO_PIN_7
#define NMES_ACU_CS_GPIO_Port GPIOB
#define CHARGER_DETECT_Pin GPIO_PIN_9
#define CHARGER_DETECT_GPIO_Port GPIOB

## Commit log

2022-10-09 moved safety, connectors and ext mem to new sheets
    [Connectors.kicad_sch, Memory.kicad_sch, NMOS_PullDown.kicad_sch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]
2022-10-10 finished remaking whole schematic
    [Communication.kicad_sch, Connectors.kicad_sch, IsolatedCommunication.kicad_sch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]
2022-10-10 finished remaking the schematic
    [Communication.kicad_sch, IsolatedCommunication.kicad_sch, IsolatedMeasurement.kicad_sch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]
2022-10-11 added external firmware to repo, add usb connector (molex 4pin 90deg) on schematic
    [Connectors.kicad_sch, M80-8661022.stp, Measurements.kicad_sch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]
2022-10-11 added additional USB port and overall board update
    [Communication.kicad_sch, Connectors.kicad_sch, IsolatedCommunication.kicad_sch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]
2022-10-11 sync, cuz not much was changed
    [Communication.kicad_sch, PUTM_EV_BMS_HV_Master_2021.kicad_pcb]
2022-10-11 switched all screw terminals for corresponding molexes n-pins 90 deg
    [Connectors.kicad_sch, IsolatedMeasurement.kicad_sch, NMOS_PullDown.kicad_sch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]
2022-10-18 fixed HV measurement
    [Connectors.kicad_sch, IsolatedMeasurement.kicad_sch, Measurements.kicad_sch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]
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2022-10-24 changed the logic behind the error latch circuit and added some 3d models for used harwin connectors
    [Connectors.kicad_sch, IsolatedMeasurement.kicad_sch, M80-8420345.stp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]
2022-10-25 added discharge resistor to latch circuit
    [PUTM_EV_BMS_HV_Master_2021.kicad_sch, Safeties.kicad_sch]
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2022-10-26 changed d flip flop to a or gate based latch
    [PUTM_EV_BMS_HV_Master_2021.kicad_sch, Safeties.kicad_sch]
2022-11-08 erased all traces, finished USB section, started HV section, swapped most footprints of R to be of the same type 0603 similary with caps (where it could be done), swapped optos for those used in Smar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
    [Communication.kicad_sch, Connectors.kicad_sch, IsolatedMeasurement.kicad_sch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]
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2022-11-08 minor HV section change
    [PUTM_EV_BMS_HV_Master_2021.kicad_pcb]
2022-11-08 HV section fix - forgot about capacitors
    [PUTM_EV_BMS_HV_Master_2021.kicad_pcb]
2022-11-08 3d models update, more work on pcb
    [ALDP105W.stp, AM1LS-NZ.step, AMC1311BDWVR.step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]
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2022-11-09 finished pcb layout, started routing, changed 2 layered board to 4 layered'
    [Communication.kicad_sch, Connectors.kicad_sch, IsolatedCommunication.kicad_sch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]
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2022-11-11 resized board and added some visual info
    [PUTM_EV_BMS_HV_Master_2021.kicad_pcb]
2022-11-11 added missing led for safety indication
    [IsolatedCommunication.kicad_sch, IsolatedMeasurement.kicad_sch, NMOS_PullDown.kicad_sch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]
2022-11-11 remade pcb so it fits into 100 x 100 mm and some minor modifications
    [Measurements.kicad_sch, NMOS_PullDown.kicad_sch, PUTM_EV_BMS_HV_Master_2021.kicad_pcb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]
2022-11-14 schematic override, just cuz
    [Communication.kicad_sch, Connectors.kicad_sch, HP_NMOS_PullDown.kicad_sch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]
2022-11-14 pcb sync, half the new new new layout is done
    [PUTM_EV_BMS_HV_Master_2021.kicad_pcb]
2022-11-22 changed HV measurements from isolated opamp to isolated ADC with isolated spi communication, changed safety laatching from mosfet back to relay
    [ADUM7440ARQZ.stp, Connectors.kicad_sch, IsolatedMeasurement.kicad_sch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]
2022-11-25 changed the 1V voltage ref made from RL circuit to low noise, 0.1% error 1.024 V ref gen, and changed the opamp used for current sensor feedback filtration to a high precision low drift opamp
    [ADA4505-1ARJZ-R7.stp, Connectors.kicad_sch, IsolatedMeasurement.kicad_sch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]
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2022-12-11 board sync and measurments section adjustments
    [IsolatedMeasurement.kicad_sch, Measurements.kicad_sch, PUTM_EV_BMS_HV_Master_2021.kicad_sch]
2022-12-13 measurments section changes, sorted components on the board into groups, changed main connector and added seprate for AIRs, added IMD PWM input as well as AIR fault detection
    [AP7365-33YRG-13.stp, Connectors.kicad_sch, HP_NMOS_PullDown.kicad_sch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]
2022-12-14 hv elem positioning update'
    [HP_NMOS_PullDown.kicad_sch, Opto2CH.kicad_sch, PUTM_EV_BMS_HV_Master_2021.kicad_pcb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]
2022-12-15 changed few connectors, finished board HV section and other minor changes
    [Connectors.kicad_sch, HP_NMOS_PullDown.kicad_sch, IsolatedCommunication.kicad_sch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]
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2023-01-14 ground plane fix
    [PUTM_EV_BMS_HV_Master_2021.kicad_pcb]
2023-01-16 board layout changes, moved USB from seprate connector to the main connector, moved optos to the bootom right corner, moved IMD signal and air detection to a seprate connector
    [Connectors.kicad_sch, HP_NMOS_PullDown.kicad_sch, IsolatedCommunication.kicad_sch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]
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2023-05-04 bigger board, distinct HV/LV and isolation, some schematic changes
    [Communication.kicad_sch, Connectors.kicad_sch, M80-5L10642MC.stp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]
2023-05-09 major changes: conn, fans, inputs and others
    [Communication.kicad_sch, Connectors.kicad_sch, Fan_drivers.kicad_sch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]
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2023-05-11 PCB routing 50-70% done
    [Communication.kicad_sch, Connectors.kicad_sch, PUTM_EV_BMS_HV_Master_2021.kicad_pcb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]
2023-05-15 slight change to one of the fill zones and added gerbers/and bom to the git files
    [PUTM_EV_BMS_HV_Master_2021.kicad_pcb, bom.csv]
2023-05-15 slight changes and adjustments to 12V power section
    [PUTM_EV_BMS_HV_Master_2021.kicad_pcb]
2023-05-17 WęGoRz AfTeR rEvIeW cOmMiT
    [Connectors.kicad_sch, IsolatedCommunication.kicad_sch, IsolatedMeasurement.kicad_sch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]
2023-05-17 via-s stormed the capitalgit status!
    [Connectors.kicad_sch, PUTM_EV_BMS_HV_Master_2021.kicad_pcb, bom.csv]
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2023-06-25 poprawka schematu dziwny bug z gerberami/kicadem przy wylewaniu tego samego neta z różnymi priorytetami i zmiana r_array z 5 (bo takich nie da się kupić XD na 8
    [Connectors.kicad_sch, PUTM_EV_BMS_HV_Master_2021.kicad_pcb]
2023-07-20 added LTC lib insitu
    [PUTM_EV_BMS_HV_Master_2021.kicad_pcb]
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2023-07-22 further work on ltc manager
    [PUTM_EV_BMS_HV_Master_2021.kicad_pcb, PUTM_EV_BMS_HV_Master_2021.kicad_sch]
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2023-07-25 Revert "further work on ltc manager"
    This reverts commit b7f355d2cc7a36195d8f9671f446215ee6a9210d.
    [PUTM_EV_BMS_HV_Master_2021.kicad_pcb, PUTM_EV_BMS_HV_Master_2021.kicad_sch]
2023-07-30 SpiController redesign & LtcContoller optimazation, deleted CAN lib copy, added concepts for most templates
    [MCP356x.hpp, PUTM_EV_BMS_HV_2023.ioc]
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2023-08-03 hardware update - fixed pcb errors
    [Communication.kicad_sch, Connectors.kicad_sch, IsolatedMeasurement.kicad_sch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]
2023-08-04 Basic Error checking ready to test.
    [Checks.hpp]
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2023-08-22 Fix temperature calc
2023-09-21 updated components to comply with new resolutions
    [2920L500_24SLDR.stp, 6-1419128-4.stp, Communication.kicad_sch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]
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2023-11-14 slight changes, changed shield's coupling resitor to a couplingcapacitor
    [Communication.kicad_sch, Connectors.kicad_sch, PUTM_EV_BMS_HV_Master_2021.kicad_pcb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]
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2024-01-03 moved hardware/main_board to hardware, deleted hardware/main_baord and hardware/connector_board, changed highside driveing transistors in acu and car HV mes to a open drain buffer for clarity and les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
    [2920L500_24SLDR.stp, 30R400UMR.stp, 6-1419128-4.stp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]
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2024-06-04 relay new driving logic, some ltc communication changes
    [Communication.kicad_sch, Connectors.kicad_sch, Fan_drivers.kicad_sch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]
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

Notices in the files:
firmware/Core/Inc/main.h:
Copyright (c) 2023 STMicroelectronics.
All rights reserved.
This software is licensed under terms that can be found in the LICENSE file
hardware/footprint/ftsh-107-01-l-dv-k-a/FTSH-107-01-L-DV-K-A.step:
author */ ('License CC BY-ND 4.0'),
